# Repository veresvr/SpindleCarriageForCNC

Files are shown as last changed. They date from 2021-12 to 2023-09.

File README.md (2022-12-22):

# Spindle Carriage For CNC
:100: Project is done!

Milling carriage for my [laser CNC](https://github.com/veresvr/LaserCNCMachine)
All drawings available here [Drawings](https://github.com/veresvr/SpindleCarriageForCNC/tree/main/Drawings/AllDrawings.pdf)

##### Rendering
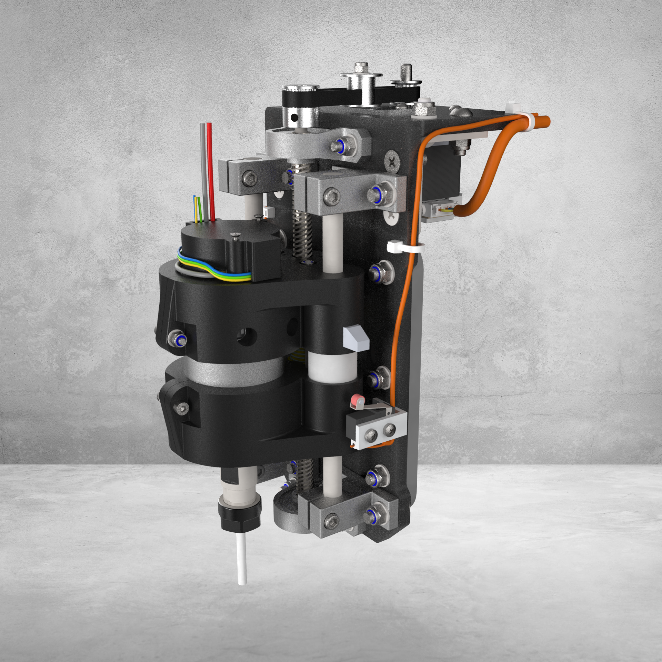
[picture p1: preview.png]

##### Assembly structure


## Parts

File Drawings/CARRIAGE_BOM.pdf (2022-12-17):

Project Spindle Carriage For CNC | Project Link GitHub (https://github.com/veresvr/SpindleCarriageForCNC)
Title cnc_milling_carriage_v1.SLDASM | Project Number 000
Designer Vladimir Tyrkin | Drawn by Vladimir Tyrkin
File CARRIAGE_BOM.xlsx
Date 17 December 2022 | Rev. 1
Dwg. | Item No. | Qty | Scem | Description | Material | Manufacturer | Part Number | Manufacturer Link | Weight | Total Weight
001 2 | | | | Linear Motion Shaft | 52100 Alloy Steel | McMaster-Carr | 5033N132 | McMaster-Carr (https://www.mcmaster.com/5033N132/) | 58.89 | 117.78
| | | | | | McMaster-Carr | 4920N11 | McMaster-Carr (https://www1.mcmaster.com/4920N11/)
| | | | | | CHINA | none | Aliexpress (https://aliexpress.ru/item/4001203233924.html?spm=a2g0o.detail.1000060.2.27ee4f0eyzRaOZ&gps-)
002 | 1 | 1 | | Lead Screw | AISI 1020 | CHINA | none | Aliexpress (https://aliexpress.ru/item/4001230970430.html?_ga=2.84334745.1452778018.1644222722-) | 62.17 | 62.17
| | | | Note: must be pair to item 2
011 1 | | | | Stepper Base | Polycarbonate (PC) | McMaster-Carr | 8574K281 | McMaster-Carr (https://www.mcmaster.com/8574K281/) | 37.88 | 37.88
| | | | Files: Drawings/parts for cnc.DWG & Drawings/parts for cnc.CDR
012 1 | | | | Vertical Plate | Polycarbonate (PC) | McMaster-Carr | 8574K281 | McMaster-Carr (https://www.mcmaster.com/8574K281/) | 120.14 | 120.14
| | | | Files: Drawings/parts for cnc.DWG & Drawings/parts for cnc.CDR
025 | | 2 | | ThreadedRodMotor | AISI 1035 Steel (SS) | McMaster-Carr | 94595A215 | McMaster-Carr (https://www.mcmaster.com/94595A215/) | 4.7 | 9.4
031 | | 1 | | TensionerBasePlate | 6061 Alloy | McMaster-Carr | 9146T14-9146T141 | McMaster-Carr (https://www.mcmaster.com/9146T14-9146T141/) | 4.5 | 4.5
032 | | 1 | | Standoff threaded round spacer | 6063-T6 | CHINA | none | Aliexpress (https://aliexpress.ru/item/32881933703.html?sku_id=12000022052244225&_ga=2.177706725.1570185891.1667054803-) | 0.48 | 0.48
081 | | 2 | | SensorMount | 6063-T6 | McMaster-Carr | 4630T135 | McMaster-Carr (https://www.mcmaster.com/4630T135/) | 2.19 | 4.38
None | | 2 | | Corner Bracket 40х40L | AISI 1035 Steel (SS) | Soberizavod | H49 | Soberizavod (https://www.soberizavod.ru/catalog/uglovye_soediniteli_seriya_20/ugolok_40kh20l_paz_6_h49/) | 49 | 98
None | | 4 | | SK8 SC8UU LINEAR RAIL ORIGINAL | Multimaterial | CHINA | none | Aliexpress (https://www.aliexpress.com/snapshot/0.html?orderId=5012744429362323&productId=32857642687) | 25 | 100
None | | 2 | | Pillow Block | Multimaterial | CHINA | none | Aliexpress (https://aliexpress.ru/item/4000176610214.html?_ga=2.180800559.940251345.1645298115-) | 37 | 74
None | | 2 | | Limit Switch | Multimaterial | DIGIKEY | none | DIGIKEY (https://www.digikey.com/en/products/detail/omron-electronics-inc-emc-div/ssg-01l2t-5/3102941) | 1.6 | 3.2
None | | 1 | | Nema 17HS4401 Stepper Motor | Multimaterial | CHINA | none | Aliexpress (https://aliexpress.ru/item/32665922113.html?_ga=2.134133639.847069604.1626648373-) | 315 | 315
None | | 5 | | Cable tie 3 mm width | Nylon 101 | McMaster-Carr | 7130K31 | McMaster-Carr (https://www.mcmaster.com/7130K31/) | 0.16 | 0.8
None | | 1 | | Belt | Rubber | CHINA | none | Aliexpress (https://aliexpress.ru/item/32971350055.html?sku_id=12000025662809083&_ga=2.102057921.1740671391.1667596887-) | 1.34 | 1.34
None | | 1 | | Heat shrink tube | Rubber | McMaster-Carr | 7496K85 | McMaster-Carr (https://www.mcmaster.com/7496K85/) | 0.12 | 0.12
None | | 1 | | Power cable 9Amp max. | Wire | McMaster-Carr | 9700T61 | McMaster-Carr (https://www.mcmaster.com/9700T61/) | 7.93 | 7.93
None | | 1 | | DC 775 Motor | Multimaterial | CHINA | none | Aliexpress (https://aliexpress.ru/item/32954455244.html?_ga=2.25715773.1065263870.1623483208-) | 314 | 314
None | | 2 | | 2GT 20Teeth Pulley | Multimaterial | CHINA | none | Aliexpress (https://aliexpress.ru/item/32969561177.html?sku_id=66708120873&_ga=2.26566781.1740671391.1667596887-) | 5.11 | 10.22
None | | 1 | | ER11 collet | Multimaterial | CHINA | none | Aliexpress (https://aliexpress.ru/item/33009204061.html?_ga=2.95643420.1065263870.1623483208-) | 49 | 49
None | | 1 | | Pulley 20T W10 B5 With Teeth | Multimaterial | CHINA | none | Aliexpress (https://aliexpress.ru/item/1005003836633631.html?sku_id=12000027307595864) | 10 | 10
None | | 4 | | LM8UU Lineare bearing | Multimaterial | CHINA | none | Aliexpress (https://aliexpress.ru/item/32317938156.html?_ga=2.97133343.1065263870.1623483208-) | 16 | 64
None | | 1 | | Cable Top End Sensor (230mm) | Multimaterial | McMaster-Carr | 9697T1 | McMaster-Carr (https://www.mcmaster.com/9697T1/) | 3.05 | 3.05
None | | 1 | | Cable Bottom End Sensor (290mm) | Multimaterial | McMaster-Carr | 9697T1 | McMaster-Carr (https://www.mcmaster.com/9697T1/) | 2.29 | 2.29
None | | 1 | | 3 CIRCUIT RECEPTACLE MOLEX | Multimaterial | MOUSER | none | Mouser (https://eu.mouser.com/ProductDetail/Molex/39-01-4031?qs=pAYFZ4D%2FDKsfbhxQKf4bKg%3D%3D) | 1 | 1
None | 2 | 1 | | Movement Nut | Brass | CHINA | none | Aliexpress (https://aliexpress.ru/item/32317938156.html?_ga=2.97133343.1065263870.1623483208-) | 11.5 | 11.5
| | | | Note: must be pair to item 1
Total weight | 1422.2
3D printed parts
021 | 1 | Bottom motor cover | PET-G | McMaster-Carr | 3462N1 | McMaster-Carr (https://www.mcmaster.com/3462N1/) | 93 | 93
| | File: FilesForPrint/Bottom motor cover.STL
022 | 1 | Top motor cover | PET-G | McMaster-Carr | 3462N1 | McMaster-Carr (https://www.mcmaster.com/3462N1/) | 87.98 | 87.98
| | File: FilesForPrint/Top motor cover.STL
024 | 2 | Spacer | PET-G | McMaster-Carr | 3462N1 | McMaster-Carr (https://www.mcmaster.com/3462N1/) | 5.97 | 11.94
| | File: FilesForPrint/Spacer.STL
026 1 | | Cable holder | PET-G | McMaster-Carr | 3462N1 | McMaster-Carr (https://www.mcmaster.com/3462N1/) | 1.21 | 1.21
| | File: FilesForPrint/WiresHolder.STL
Total weight | 194.13
Page 1 of 2 | 12/17/2022 16:02

Dwg. | Item
No. | Scem | Description | Material | Manufacturer | Part Number | Manufacturer Link
Weight

Total
Weight Qty

Screws
None | 1 | Self Tap. Cross recessed Screw 2.6x10mm | AISI 304 | CHINA | none | Aliexpress (https://aliexpress.ru/item/33040347870.html?spm=a2g0s.9042311.0.0.274233edM7ZVS8) | 0.23 | 0.23
None | 6 | M3 NYLOC DIN 985 | AISI 304 | CHINA | none | Aliexpress (https://www.mcmaster.com/nuts/locknuts/metric-18-8-stainless-steel-nylon-insert-locknuts/) | 0.65 | 3.9
None | 4 | M4 NYLOC DIN 985 | AISI 304 | McMaster-Carr | none | McMaster-Carr (https://www.mcmaster.com/nuts/locknuts/metric-18-8-stainless-steel-nylon-insert-locknuts/) | 1.29 | 5.16
None | 22 | M5 NYLOC DIN 985 | AISI 304 | McMaster-Carr | none | McMaster-Carr (https://www.mcmaster.com/nuts/locknuts/metric-18-8-stainless-steel-nylon-insert-locknuts/) | 1.6 | 35.2
None | 6 | Low Profile Hex Screw M5x30 | AISI 1035 Steel (SS) | CHINA | none | Aliexpress (https://aliexpress.ru/item/4001232036314.html?_ga=2.27484988.1065263870.1623483208-) | 3.63 | 21.78
| | | | McMaster-Carr | none | McMaster-Carr (https://www.mcmaster.com/90358A119/)
None | 4 | Rounded Head Thread-Forming Screw M3x20mm | 18-8 Stainless Steel | McMaster-Carr | 99461A947 | McMaster-Carr (https://www.mcmaster.com/99461A947/) | 0.73 | 2.92
None | 1 | M5x20 DIN 7991, ISO 10642 | 18-8 Stainless Steel | McMaster-Carr | 92125A214 | McMaster-Carr (https://www.mcmaster.com/92125A214/) | 3.162 | 3.162
None | 4 | M5x16 DIN 7991, ISO 10642 | 18-8 Stainless Steel | McMaster-Carr | 92125A212 | McMaster-Carr (https://www.mcmaster.com/92125A212/) | 2.65 | 10.6
None | 4 | ISO 4762 M4 x 20 - 20N | 18-8 Stainless Steel | McMaster-Carr | 91292A121 | McMaster-Carr (https://www1.mcmaster.com/91292A121/) | 2.65 | 10.6
None | 17 | Washer DIN 125 - A 5.3 | Zinc Plated Steel | McMaster-Carr | none | McMaster-Carr (https://www1.mcmaster.com/standard-washers/washers-4/washers-5/metric-general-purpose-washers/) | 0.44 | 7.48
None | 4 | Washer DIN 125 - A 4.3 | Zinc Plated Steel | McMaster-Carr | none | McMaster-Carr (https://www1.mcmaster.com/standard-washers/washers-4/washers-5/metric-general-purpose-washers/) | 0.3 | 1.2
None | 7 | Washer DIN 125 - A 3.2 | Zinc Plated Steel | McMaster-Carr | 91166A210 | McMaster-Carr (https://www1.mcmaster.com/91166A210/) | 0.12 | 0.84
None | 2 | ISO 4762 M3 x 16 - 16N | 18-8 Stainless Steel | McMaster-Carr | none | McMaster-Carr (https://www.mcmaster.com/screws/socket-head-screws/socket-head-screws-6/18-8-stainless-steel-socket-head-screws-11/system-of-measurement~metric/) | 1.16 | 2.32
None | 2 | ISO 7380 - M3 x 10 - 10N | 316 Stainless Steel | McMaster-Carr | 90943A113 | McMaster-Carr (https://www.mcmaster.com/90943A113/) | 0.7 | 1.4
None | 4 | ISO 7380 - M5 x 16 - 16N | 18-8 Stainless Steel | McMaster-Carr | 92095A212 | McMaster-Carr (https://www.mcmaster.com/92095A212/) | 2.9 | 11.6
None | 3 | ISO 7380 - M3 x 8 - 8N | 18-8 Stainless Steel | McMaster-Carr | 92095A181 | McMaster-Carr (https://www1.mcmaster.com/92095A181/) | 0.6 | 1.8
None | 3 | ISO 7046-1 - M3 x 8 - Z - 8N | 18-8 Stainless Steel | McMaster-Carr | 92010A118 | McMaster-Carr (https://www1.mcmaster.com/92010A118/) | 0.47 | 1.41
None | 4 | ISO 7046-1 - M3 x 10 - Z - 10N | 18-8 Stainless Steel | McMaster-Carr | For DIN 965: 92010A120 | McMaster-Carr (https://www1.mcmaster.com/92010A120/) | 0.53 | 2.12
None | 4 | DIN EN ISO 7045 - M3 x 10 - Z - 10N | Zinc-Plated Steel | McMaster-Carr | 92005A120 | McMaster-Carr (https://www1.mcmaster.com/92005A120/) | 1.27 | 5.08
None | 4 | ISO 7046-1 - M5 x 20 - Z - 20N | Zinc-Plated Steel | McMaster-Carr | For DIN 965: 91420A328 | McMaster-Carr (https://www.mcmaster.com/91420A328/) | 2.86 | 11.44
Total weight | 140.24
Page 2 of 2 | 12/17/2022 16:02

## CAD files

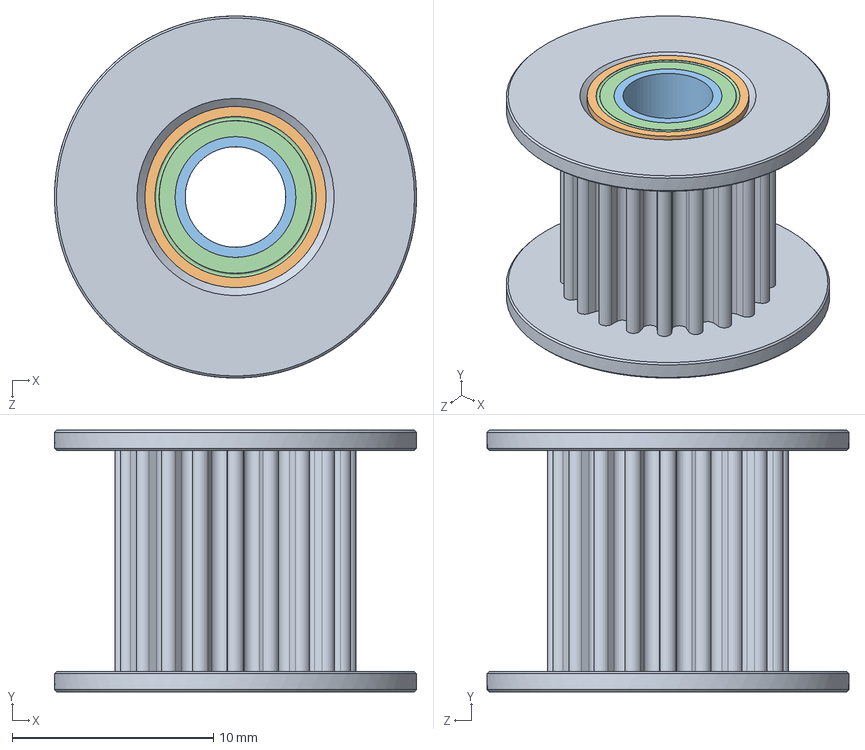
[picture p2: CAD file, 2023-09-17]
3D/GT2 Idler Pulley, Configurable.SLDASM
18.0 x 13.0 x 18.0 mm
Body, GT2 Idler Pulley, Configurable
Bearing Outer Ring, GT2 Idler Pulley, Configurable x 2
Bearing Inner Ring, GT2 Idler Pulley, Configurable x 2
Bearing Seal, GT2 Idler Pulley, Configurable x 4
Bearing Ball, GT2 Idler Pulley, Configurable x 22

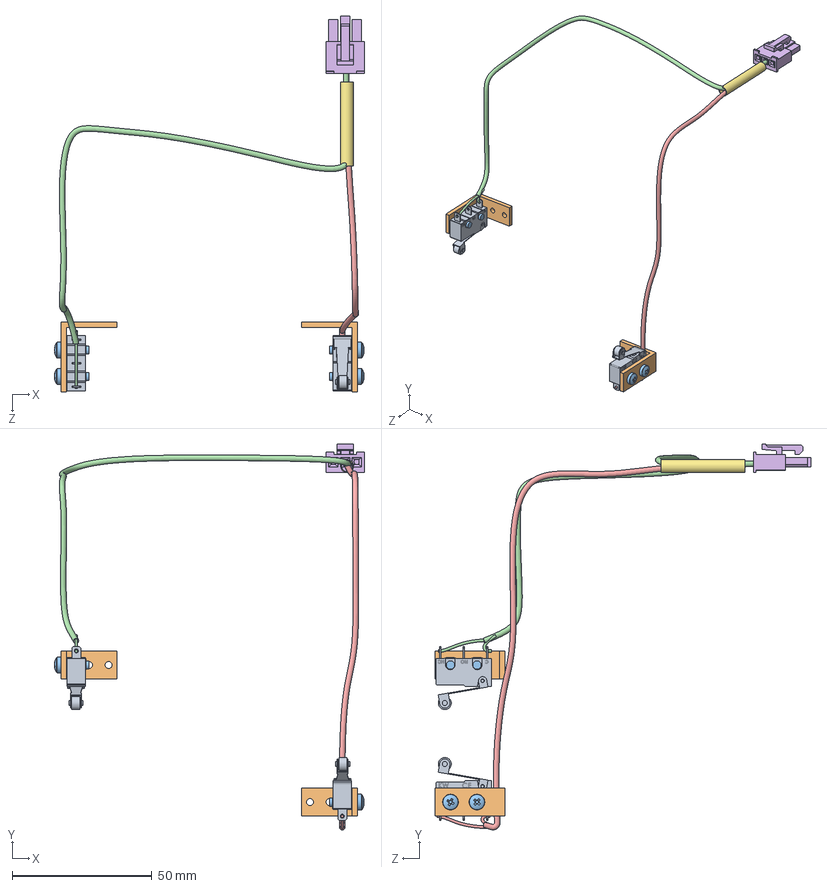
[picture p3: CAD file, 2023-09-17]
3D/SensorsAssembly.SLDASM
110.8 x 138.0 x 134.4 mm
Limit Switch x 2
SensorMount x 2
pan head cross recess screw_din x 4
CableTopEndSensor^SensorsAssembly
CableBottomEndSensor^SensorsAssembly
3 CIRCUIT RECEPTACLE MOLEX
Heat-Shrink Tube^SensorsAssembly

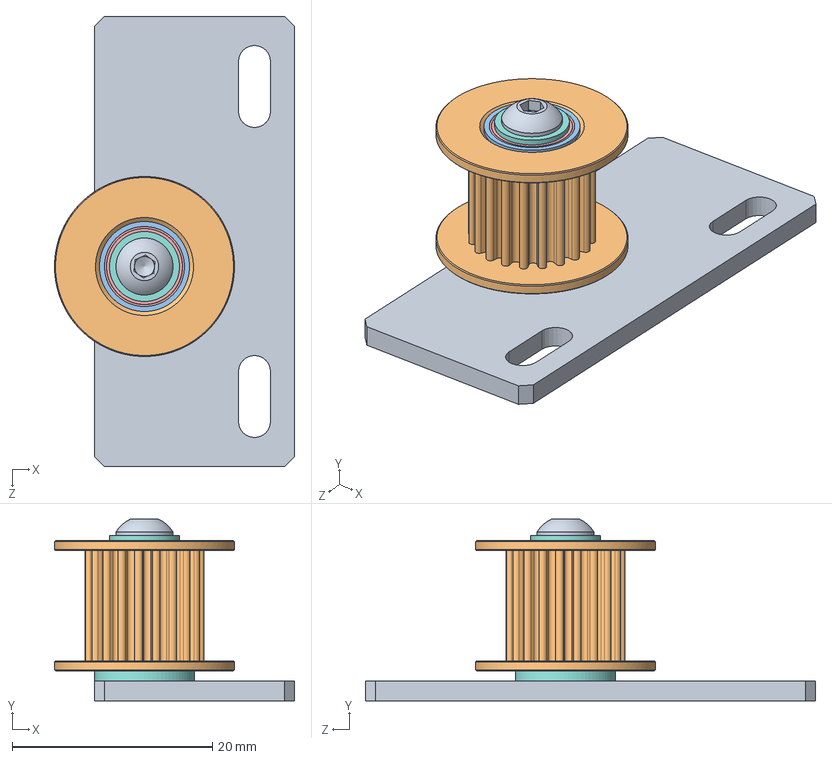
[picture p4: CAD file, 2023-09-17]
3D/Tensioner.SLDASM
24.0 x 18.1 x 45.0 mm
TensionerBasePlate
Body, GT2 Idler Pulley, Configurable
Bearing Outer Ring, GT2 Idler Pulley, Configurable x 2
Bearing Inner Ring, GT2 Idler Pulley, Configurable x 2
Bearing Seal, GT2 Idler Pulley, Configurable x 4
Bearing Ball, GT2 Idler Pulley, Configurable x 22
countersunk flat head cross recess screw_iso
plain washer grade a_din x 2
socket button head screw_iso
Standoff threaded round spacer

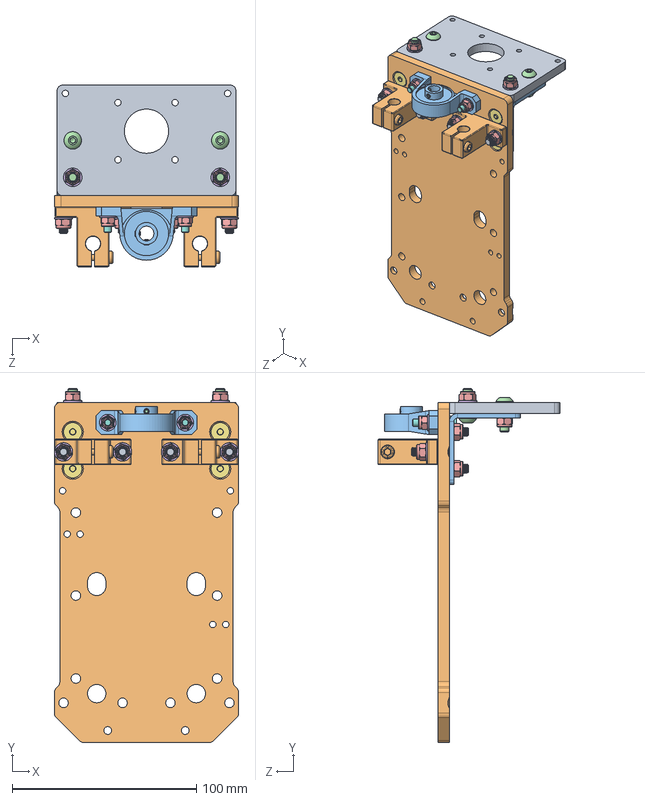
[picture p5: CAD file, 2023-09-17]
3D/CarriageBase.SLDASM
100.0 x 192.0 x 98.6 mm
Stepper Base
Vertical Plate
Corner Bracket 40х40L x 2
socket button head screw_iso x 4
Nyloc nut St_Steel A2 ISO M2_5-M36 x 14
plain washer grade a_din x 8
92125A212_18-8 Stainless Steel Hex Drive Flat Head Screw x 4
socket head cap screw_iso x 2
92125A214_18-8 Stainless Steel Hex Drive Flat Head Screw x 4
SK8 SC8UU LINEAR RAIL ORIGINAL x 2
Pillow Block KP08
socket set screw flat point_iso x 2

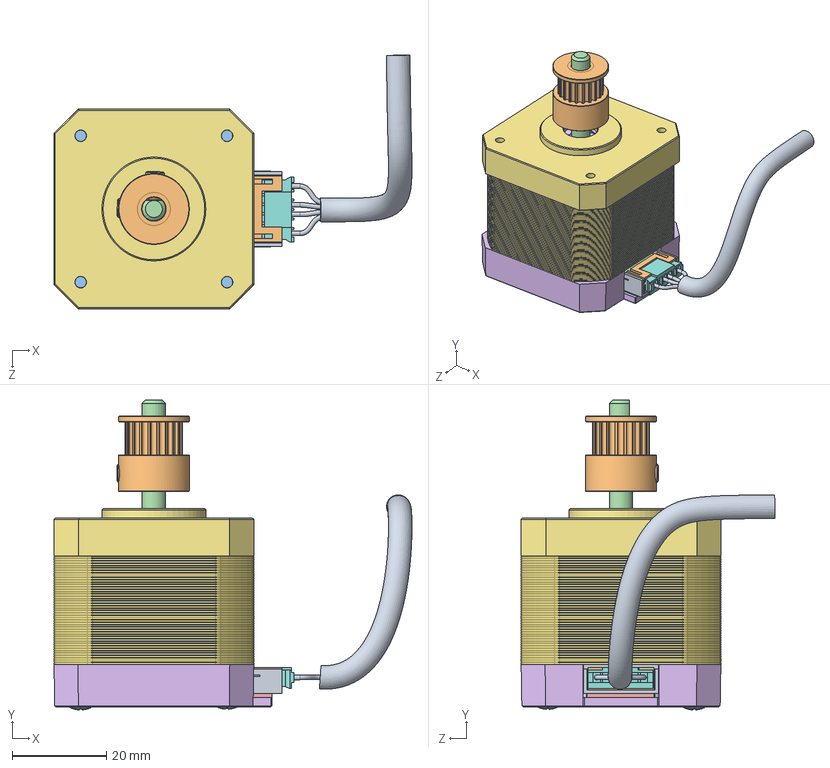
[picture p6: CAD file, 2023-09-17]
3D/Stepper Assembly.SLDASM
75.8 x 65.6 x 53.7 mm
BS 3469 - 02 - 5 x 16 x 5^Nema 17HS4401 Stepper Motor x 2
Nema 17 Plastic Spacer 2^Nema 17HS4401 Stepper Motor
Nema 17 Plastic Spacer 1
Nema 17 shaft^Nema 17HS4401 Stepper Motor
ANSI B27.7 - 5, E^Nema 17HS4401 Stepper Motor
Nema 17 Base Cap^Nema 17HS4401 Stepper Motor
Nema 17 Central Spacer^Nema 17HS4401 Stepper Motor
Nema 17 Stator Face^Nema 17HS4401 Stepper Motor
Nema 17 plastic^Nema 17HS4401 Stepper Motor
S6B-PH-K-S^Nema 17HS4401 Stepper Motor
EN ISO 7045 - M3 x 25(1)^Nema 17HS4401 Stepper Motor x 4
Nema 17 plastic protector^Nema 17HS4401 Stepper Motor
Nema 17 PCB^Nema 17HS4401 Stepper Motor
Nema 17 Sprung Washer^Nema 17HS4401 Stepper Motor
17HS4401-Part5^Nema 17HS4401 Stepper Motor
PHR-6-connector
Part1^CableStepperY_Stepper Assembly
2GT_20T_Toothed_5mmBore

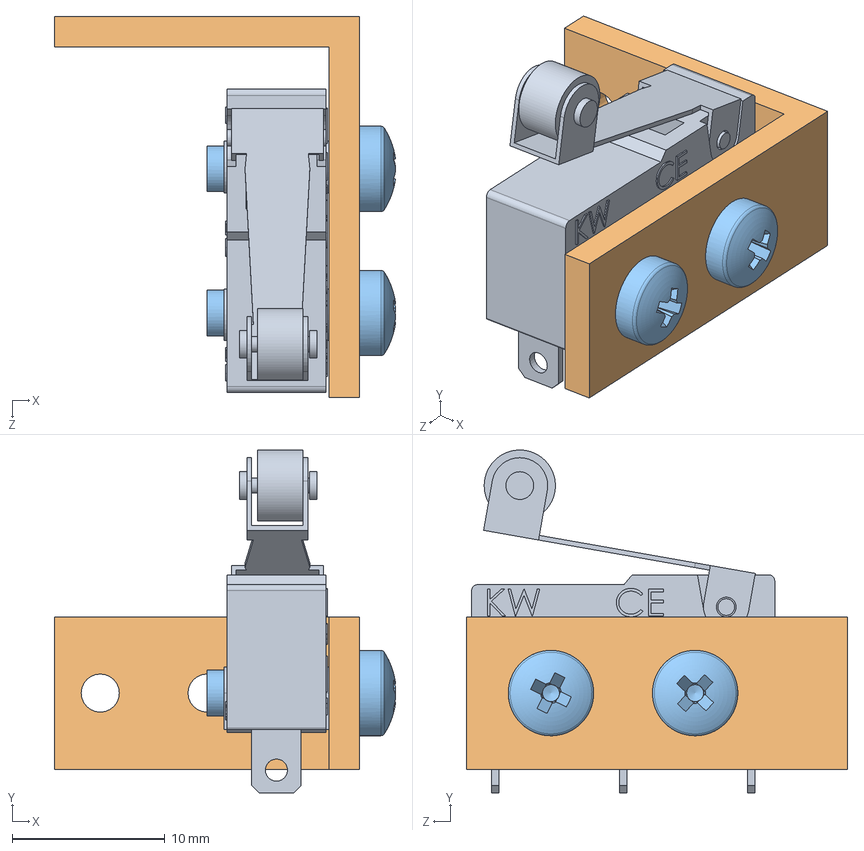
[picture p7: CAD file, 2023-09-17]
3D/EndSensorModule.SLDASM
22.4 x 22.5 x 25.0 mm
Limit Switch
SensorMount
pan head cross recess screw_din x 2

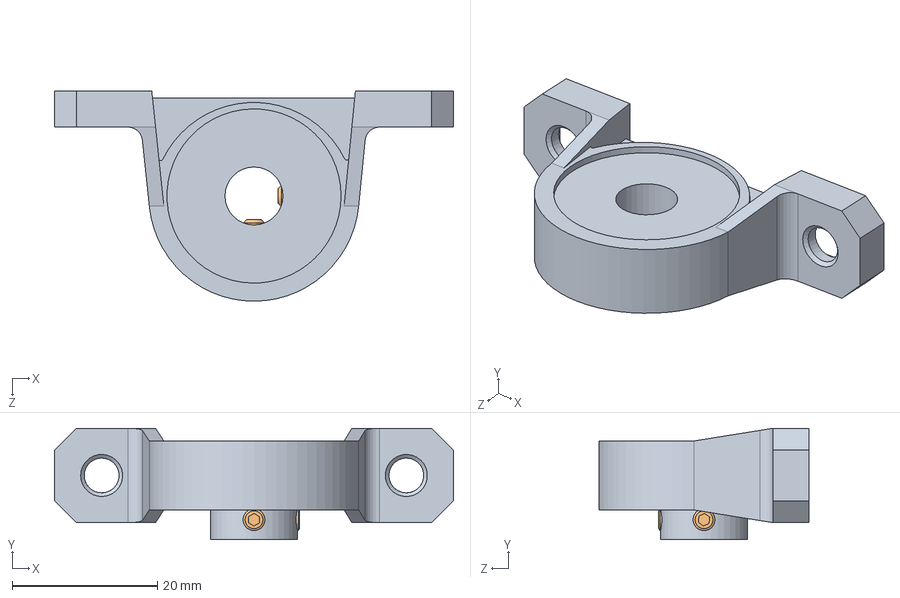
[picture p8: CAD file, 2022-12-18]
3D/PillowBlockAssembly.SLDASM
55.0 x 15.4 x 29.0 mm
Pillow Block KP08
socket set screw flat point_iso x 2

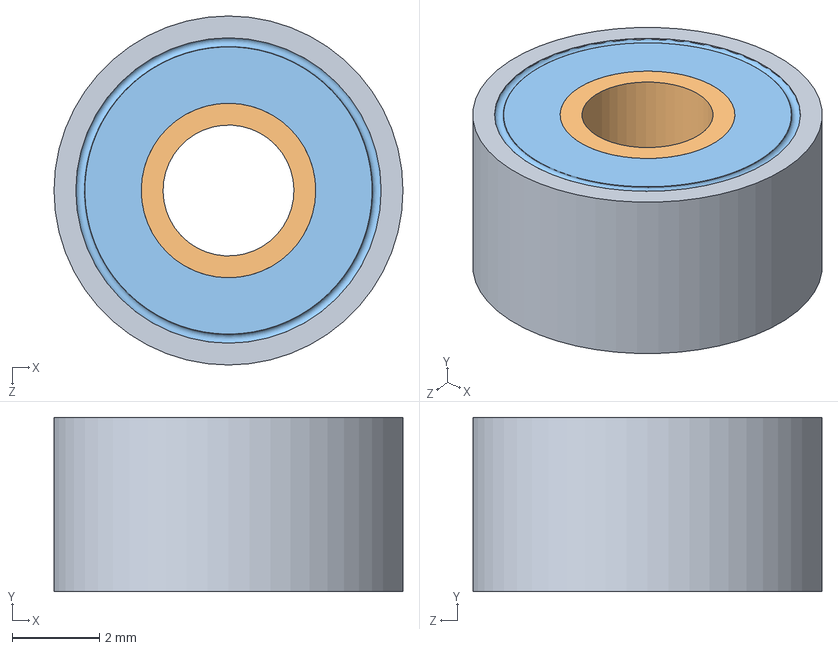
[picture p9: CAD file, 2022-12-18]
3D/Bearing Subassy, GT2 Idler Pulley, Configurable.SLDASM
8.00 x 4.00 x 8.00 mm
Bearing Outer Ring, GT2 Idler Pulley, Configurable
Bearing Inner Ring, GT2 Idler Pulley, Configurable
Bearing Seal, GT2 Idler Pulley, Configurable x 2
Bearing Ball, GT2 Idler Pulley, Configurable x 6

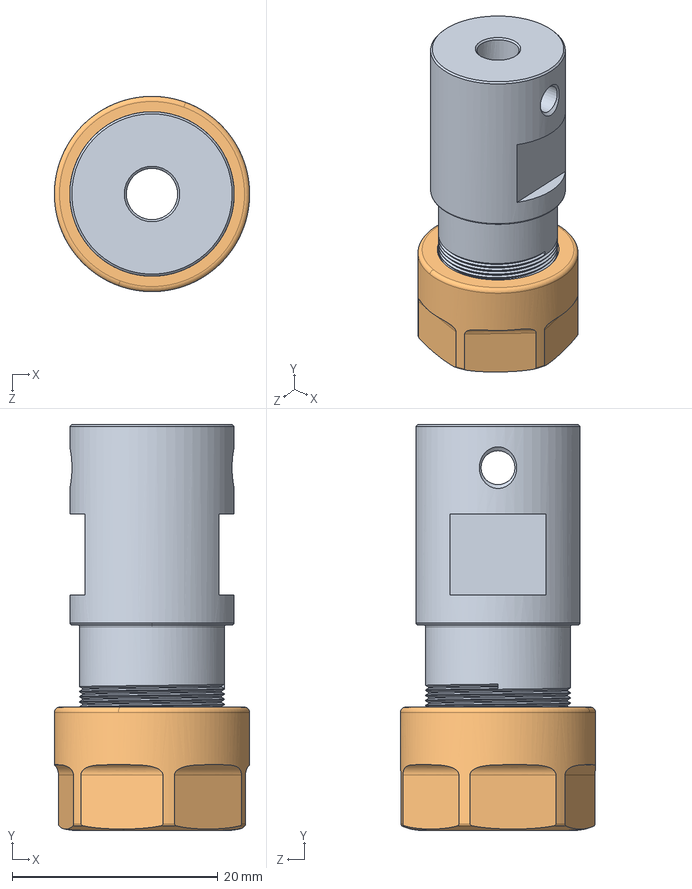
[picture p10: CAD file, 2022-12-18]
3D/ER11 collet.SLDASM
19.0 x 39.5 x 19.0 mm
ER11 - Collet Chuck
ER11 - Nut - Type A

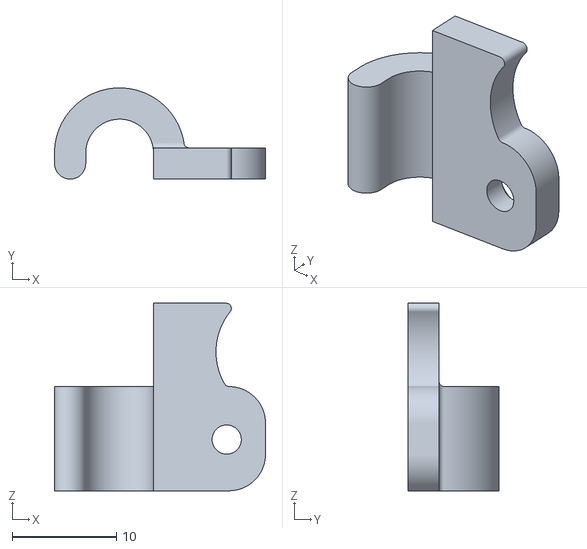
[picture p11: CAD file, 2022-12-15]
FilesForPrint/CableHolder.STL
20.3 x 8.75 x 18.0

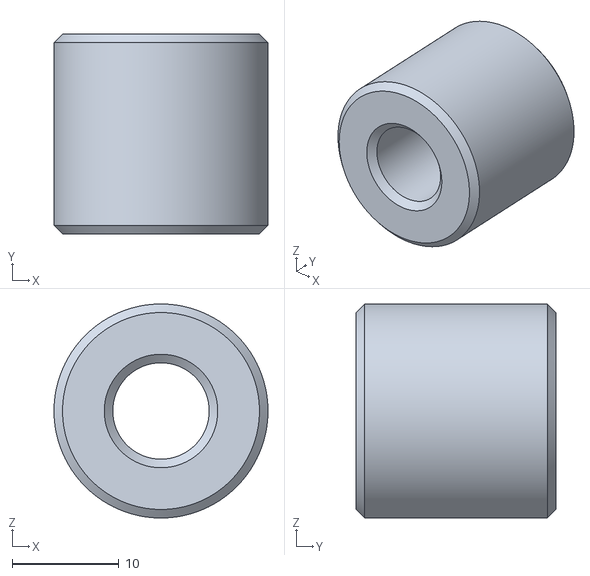
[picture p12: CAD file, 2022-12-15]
FilesForPrint/Spacer.STL
20.0 x 18.7 x 20.0

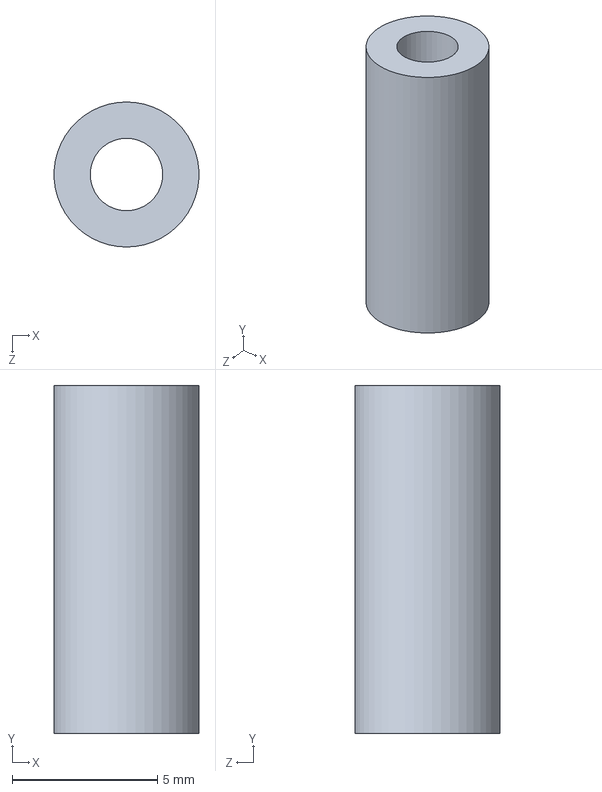
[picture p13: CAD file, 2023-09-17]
3D/Standoff threaded round spacer.SLDPRT
4.99 x 12.0 x 5.00 mm

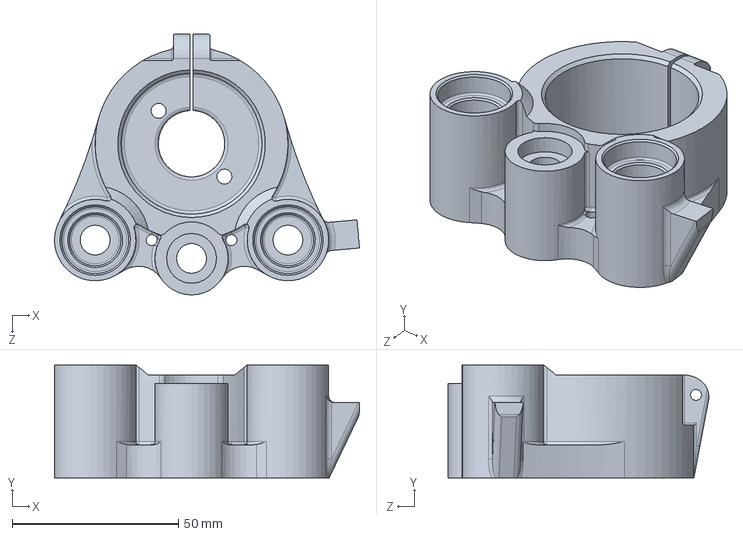
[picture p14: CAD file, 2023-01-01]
3D/Bottom motor cover.SLDPRT
91.8 x 34.0 x 78.5 mm

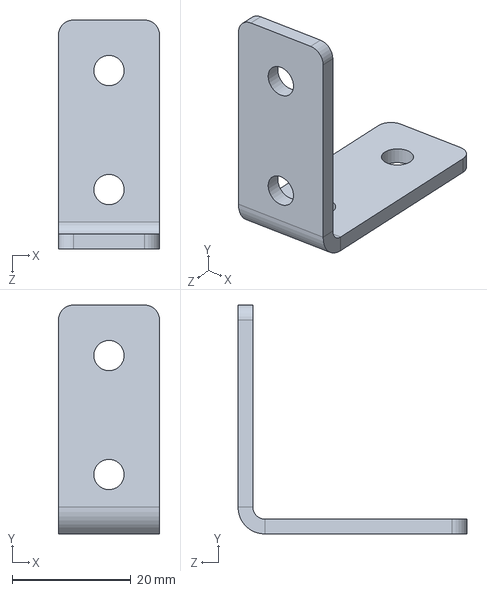
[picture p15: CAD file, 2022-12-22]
3D/Corner Bracket 40х40L.SLDPRT
17.0 x 38.5 x 38.5 mm

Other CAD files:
Drawings/parts for cnc.DWG
3D/Top motor cover.SLDPRT
3D/2GT_20T_Toothed_5mmBore.SLDPRT
3D/3 CIRCUIT RECEPTACLE MOLEX.SLDPRT
3D/92125A212_18-8 Stainless Steel Hex Drive Flat Head Screw.SLDPRT
3D/92125A214_18-8 Stainless Steel Hex Drive Flat Head Screw.SLDPRT
3D/99461A947_Phillips Rounded Head Thread-Forming Screws.SLDPRT
3D/Bearing Ball, GT2 Idler Pulley, Configurable.SLDPRT
3D/Bearing Inner Ring, GT2 Idler Pulley, Configurable.SLDPRT
3D/Bearing Outer Ring, GT2 Idler Pulley, Configurable.SLDPRT
3D/Bearing Seal, GT2 Idler Pulley, Configurable.SLDPRT
3D/Body, GT2 Idler Pulley, Configurable.SLDPRT
3D/CableHolder.SLDPRT
3D/Carriage Y_2 JustForReference.SLDPRT
3D/ER11 - Collet Chuck.SLDPRT
3D/ER11 - Nut - Type A.SLDPRT
3D/Lead Screw.sldprt
3D/Limit Switch.SLDPRT
3D/Linear Motion Shaft.SLDPRT
3D/Lineare_bearing_LMUU_serie.SLDPRT
3D/Low Profile Hex Screw M5.SLDPRT
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

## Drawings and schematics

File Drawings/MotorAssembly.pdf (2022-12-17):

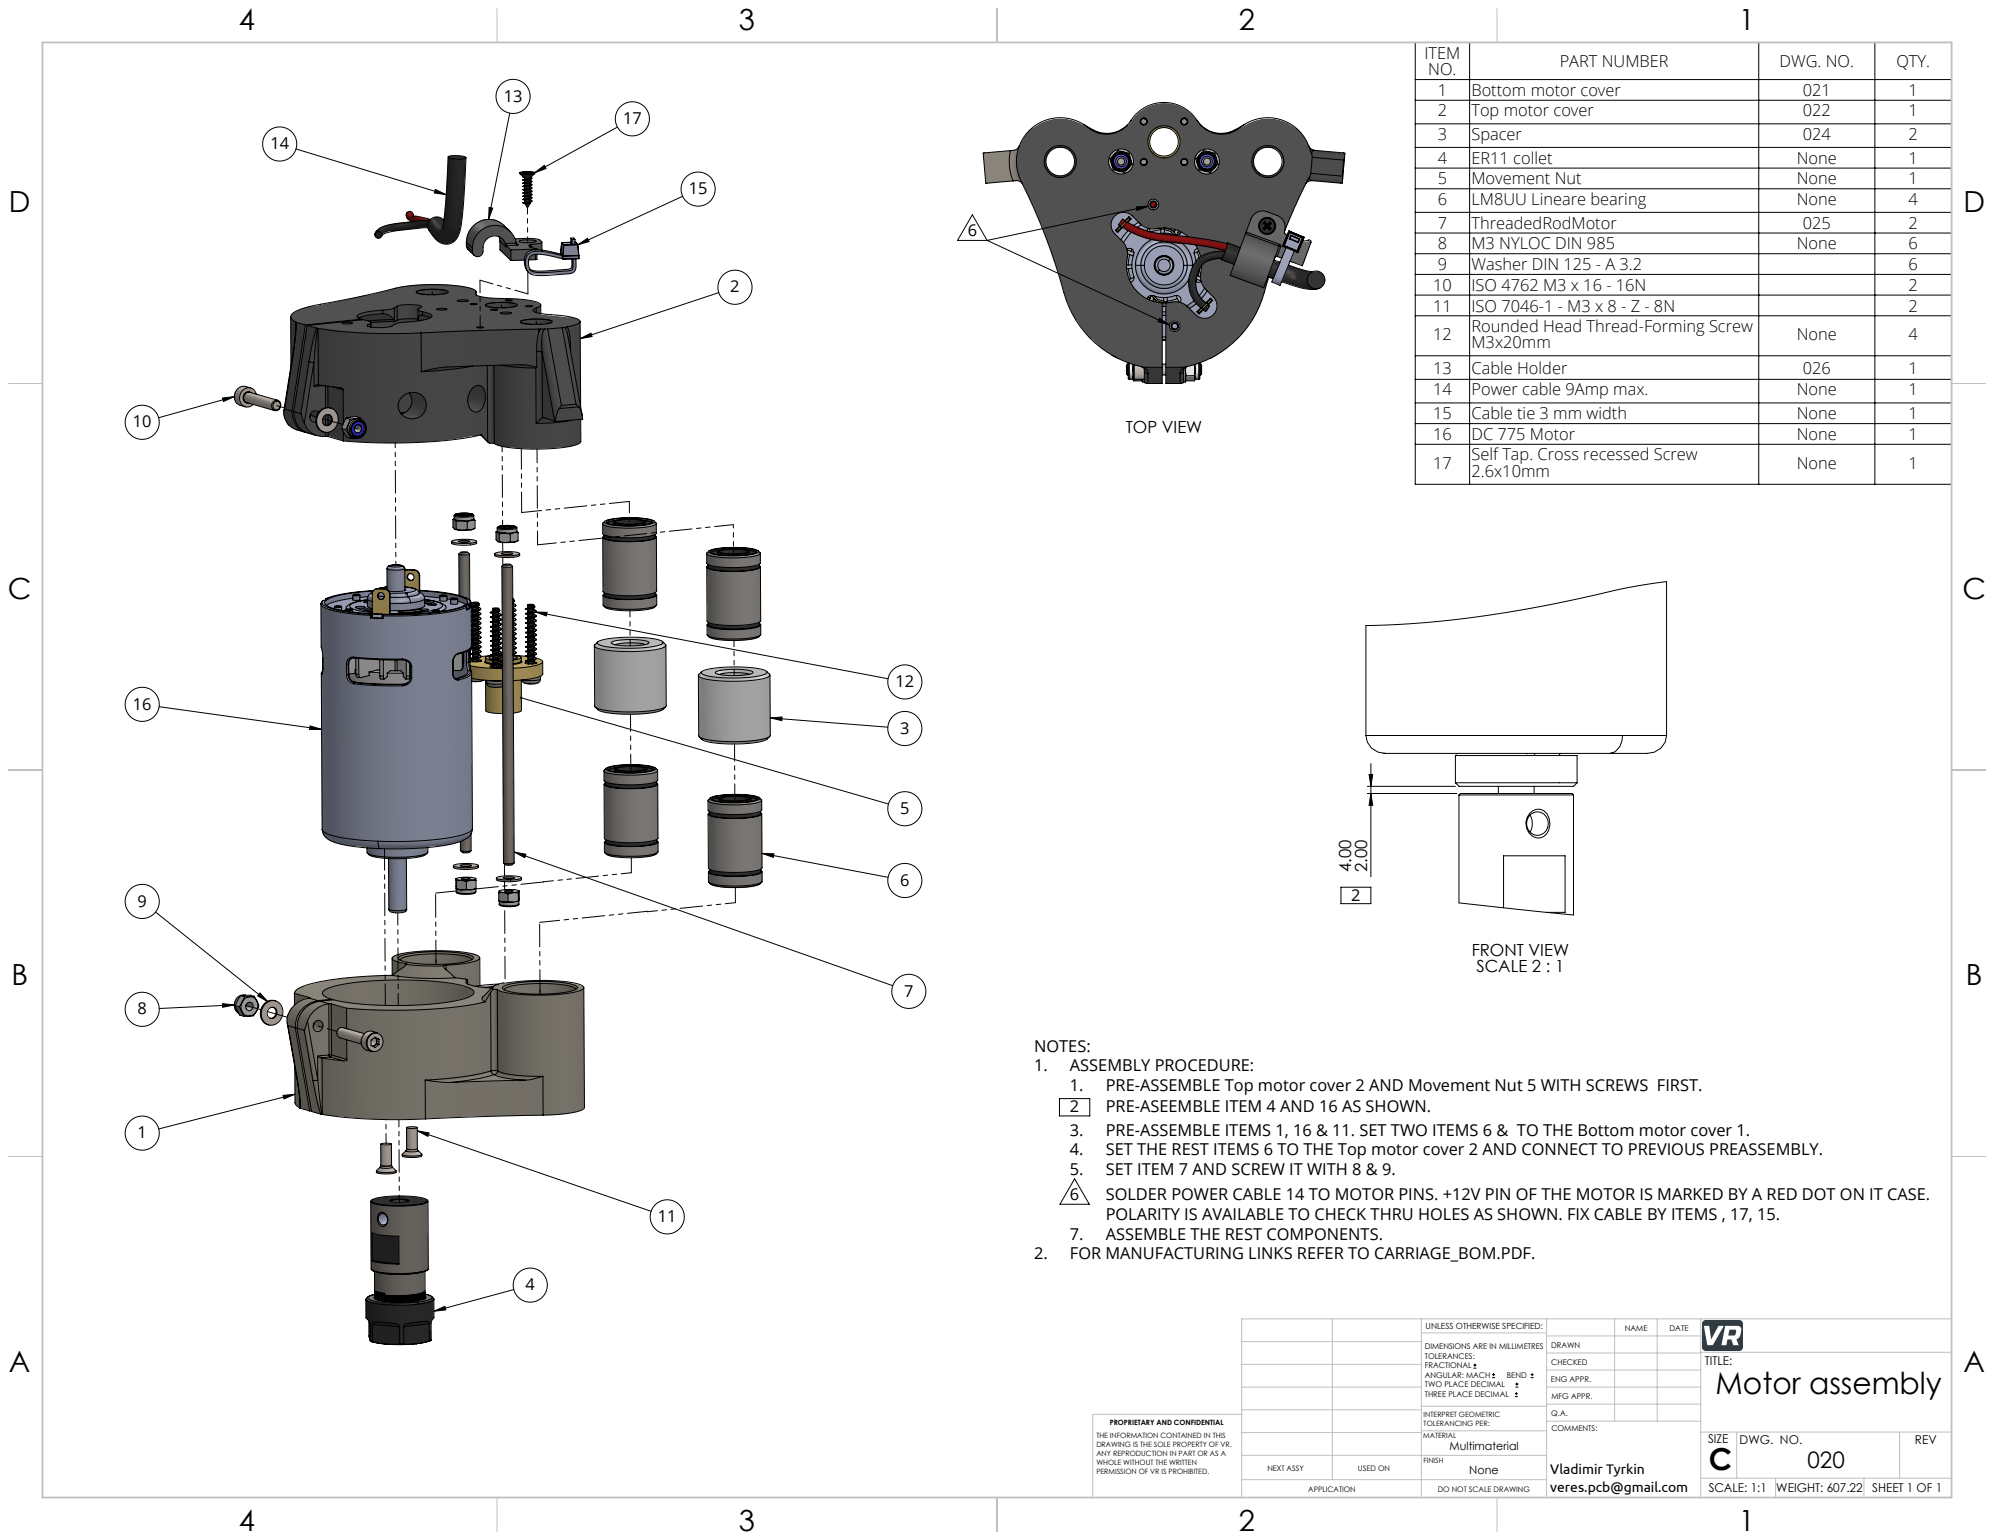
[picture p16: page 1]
TOP VIEW; FRONT VIEW SCALE 2 : 1; PRE-ASEEMBLE ITEM; SOLDER POWER CABLE 14 TO MOTOR PINS. +12V PIN OF THE MOTOR IS MARKED BY A RED DOT ON IT CASE.; PART NUMBER; DWG. NO.; QTY. 1; Bottom motor cover; Top motor cover; Spacer; ER11 collet; None; Movement Nut; LM8UU Lineare bearing; ThreadedRodMotor; M3 NYLOC DIN 985; Washer DIN 125 - A 3.2; REV; Vladimir Tyrkin

10 | ISO 4762 M3 x 16 - 16N | | 2
11 | ISO 7046-1 - M3 x 8 - Z - 8N | | 2
12 | Rounded Head Thread-Forming Screw M3x20mm | None | 4

13 | Cable Holder | 026 | 1
14 | Power cable 9Amp max. | None | 1
15 | Cable tie 3 mm width | None | 1
16 | DC 775 Motor | None | 1
17 | Self Tap. Cross recessed Screw 2.6x10mm | None | 1

NOTES:
1. ASSEMBLY PROCEDURE:
1. PRE-ASSEMBLE Top motor cover
3. PRE-ASSEMBLE ITEMS 1, 16 & 11. SET TWO ITEMS
4. SET THE REST ITEMS
5. SET ITEM
POLARITY IS AVAILABLE TO CHECK THRU HOLES AS SHOWN. FIX CABLE BY ITEMS , 17, 15
7. ASSEMBLE THE REST COMPONENTS.
2. FOR MANUFACTURING LINKS REFER TO CARRIAGE_BOM.PDF.

2 AND Movement Nut

5 WITH SCREWS FIRST.

4 AND 16 AS SHOWN.

6 & TO THE Bottom motor cover
2 AND CONNECT TO PREVIOUS PREASSEMBLY.

6 TO THE Top motor cover

7 AND SCREW IT WITH

UNLESS OTHERWISE SPECIFIED: | | NAME | DATE
DIMENSIONS ARE IN MILLIMETRES TOLERANCES: FRACTIONAL ANGULAR: MACH BEND TWO PLACE DECIMAL THREE PLACE DECIMAL | DRAWN

CHECKED | | | TITLE: Motor assembly

ENG APPR.
MFG APPR.

INTERPRET GEOMETRIC TOLERANCING PER: | Q.A.

PROPRIETARY AND CONFIDENTIAL
THE INFORMATION CONTAINED IN THIS
DRAWING IS THE SOLE PROPERTY OF VR.
ANY REPRODUCTION IN PART OR AS A
WHOLE WITHOUT THE WRITTEN
PERMISSION OF VR IS PROHIBITED.

NEXT ASSY | USED ON | None FINISH

APPLICATION | DO NOT SCALE DRAWING | | SCALE: 1:1 | WEIGHT: 607.22 | SHEET 1 OF 1

veres.pcb@gmail.com

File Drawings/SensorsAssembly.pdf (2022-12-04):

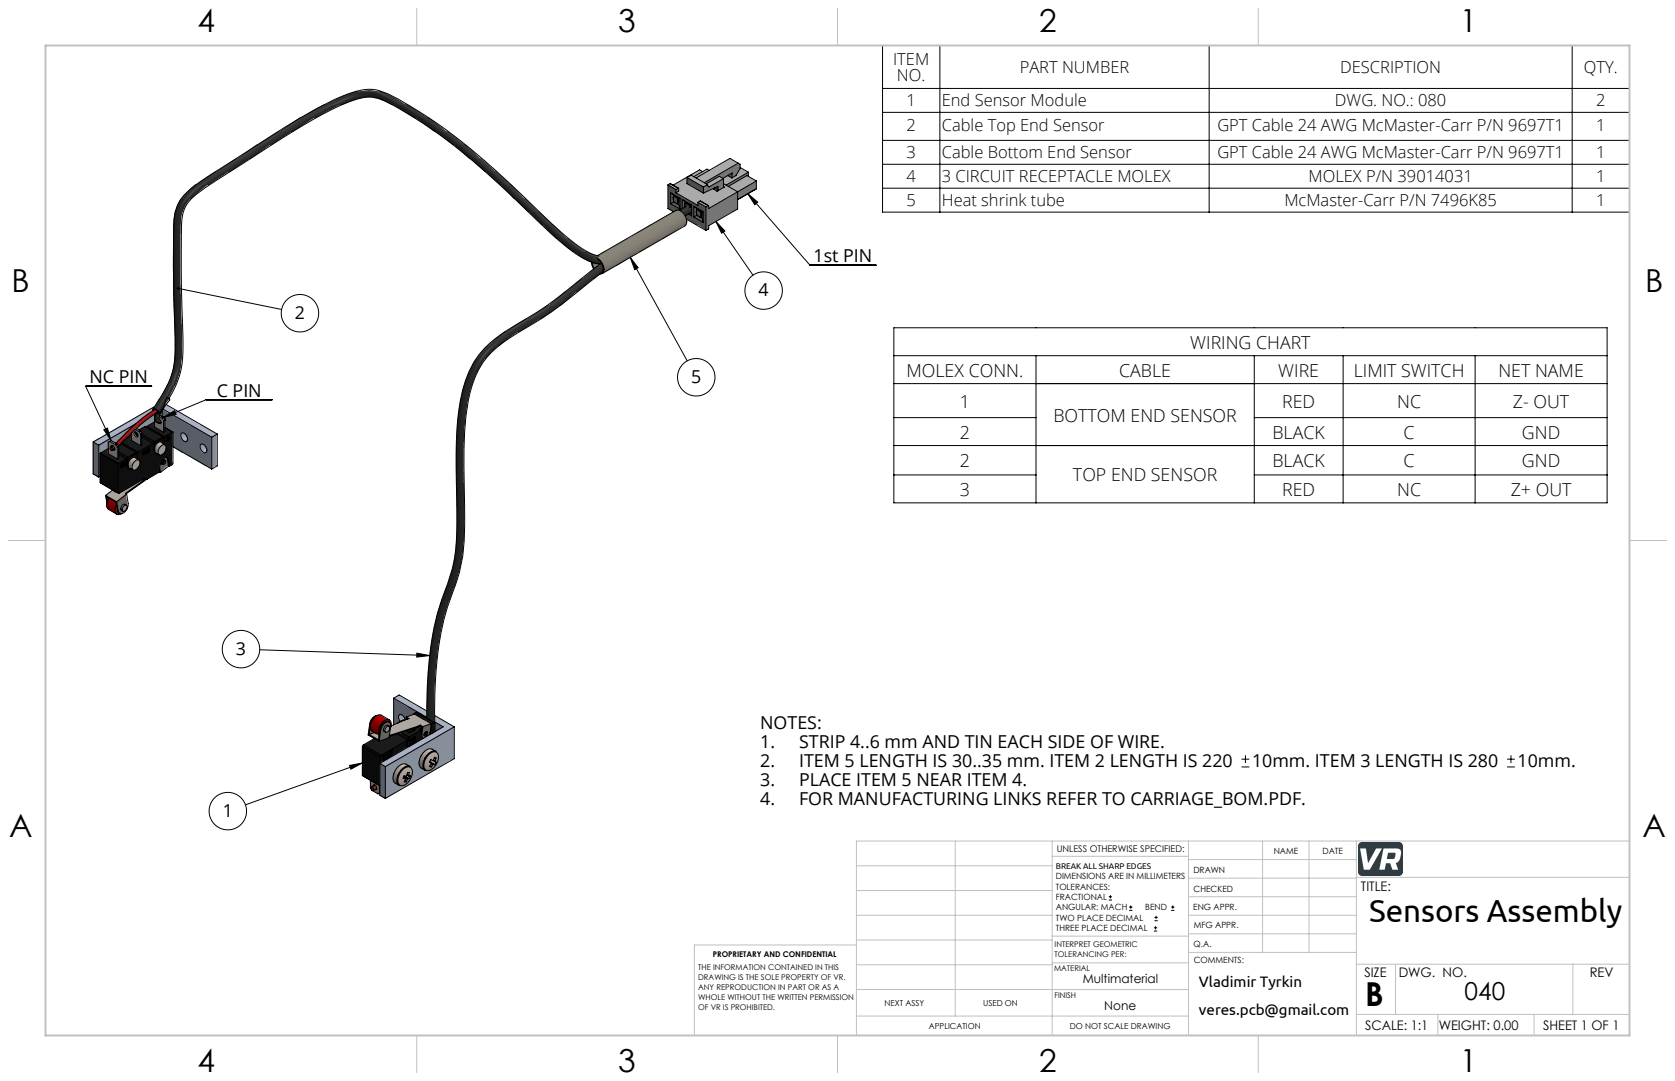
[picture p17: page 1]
1st PIN; C PIN; NC PIN; 2. ITEM 5 LENGTH IS 30..35 mm. ITEM 2 LENGTH IS 220; 10mm. ITEM 3 LENGTH IS 280; WIRING CHART; OF VR IS PROHIBITED.; veres.pcb@gmail.com; Vladimir Tyrkin

ITEM NO. | PART NUMBER | DESCRIPTION | QTY.
1 | End Sensor Module | DWG. NO.: 080 | 2
2 | Cable Top End Sensor | GPT Cable 24 AWG McMaster-Carr P/N 9697T1 | 1
3 | Cable Bottom End Sensor | GPT Cable 24 AWG McMaster-Carr P/N 9697T1 | 1
4 | 3 CIRCUIT RECEPTACLE MOLEX | MOLEX P/N 39014031 | 1
5 | Heat shrink tube | McMaster-Carr P/N 7496K85 | 1

MOLEX CONN. | CABLE | WIRE | LIMIT SWITCH | NET NAME
1 | BOTTOM END SENSOR | RED | NC | Z- OUT
2 | | BLACK | C | GND
2 | TOP END SENSOR | BLACK | C | GND
3 | | RED | NC | Z+ OUT

NOTES:
1. STRIP 4..6 mm AND TIN EACH SIDE OF WIRE.
3. PLACE ITEM 5 NEAR ITEM 4.
4. FOR MANUFACTURING LINKS REFER TO CARRIAGE_BOM.PDF.

UNLESS OTHERWISE SPECIFIED: | | NAME | DATE
BREAK ALL SHARP EDGES DIMENSIONS ARE IN MILLIMETERS TOLERANCES: FRACTIONAL ANGULAR: MACH BEND TWO PLACE DECIMAL THREE PLACE DECIMAL | DRAWN

CHECKED | | | TITLE: Sensors Assembly

ENG APPR.
MFG APPR.

INTERPRET GEOMETRIC TOLERANCING PER: | Q.A.
MATERIAL Multimaterial | | SIZE B | DWG. NO. 040 | REV

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

NEXT ASSY | USED ON | None FINISH

APPLICATION | DO NOT SCALE DRAWING | | SCALE: 1:1 | WEIGHT: 0.00 | SHEET 1 OF 1

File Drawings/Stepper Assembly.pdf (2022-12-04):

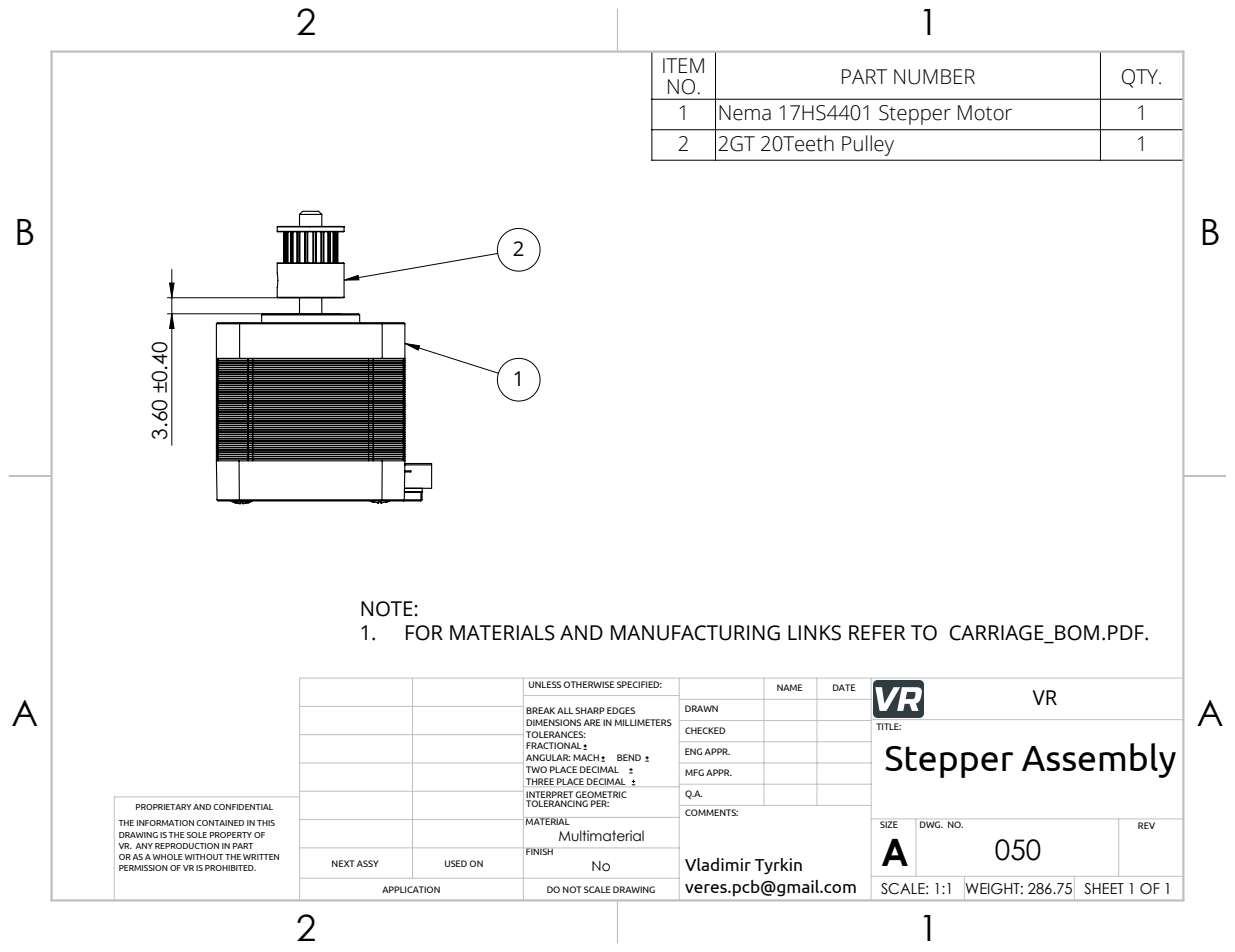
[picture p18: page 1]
PERMISSION OF VR IS PROHIBITED.; Vladimir Tyrkin

ITEM NO. | PART NUMBER | QTY.
1 | Nema 17HS4401 Stepper Motor | 1
2 | 2GT 20Teeth Pulley | 1

NOTE:
1. FOR MATERIALS AND MANUFACTURING LINKS REFER TO CARRIAGE_BOM.PDF.

UNLESS OTHERWISE SPECIFIED: | | DATE | VR NAME

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

CHECKED | | TITLE: Stepper Assembly

ENG APPR.

MFG APPR.

INTERPRET GEOMETRIC TOLERANCING PER: | Q.A.
MATERIAL Multimaterial | | SIZE A | DWG. NO. 050 | REV

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

NEXT ASSY | USED ON | FINISH No

APPLICATION | DO NOT SCALE DRAWING | | SCALE: 1:1 | WEIGHT: 286.75 | SHEET 1 OF 1

veres.pcb@gmail.com

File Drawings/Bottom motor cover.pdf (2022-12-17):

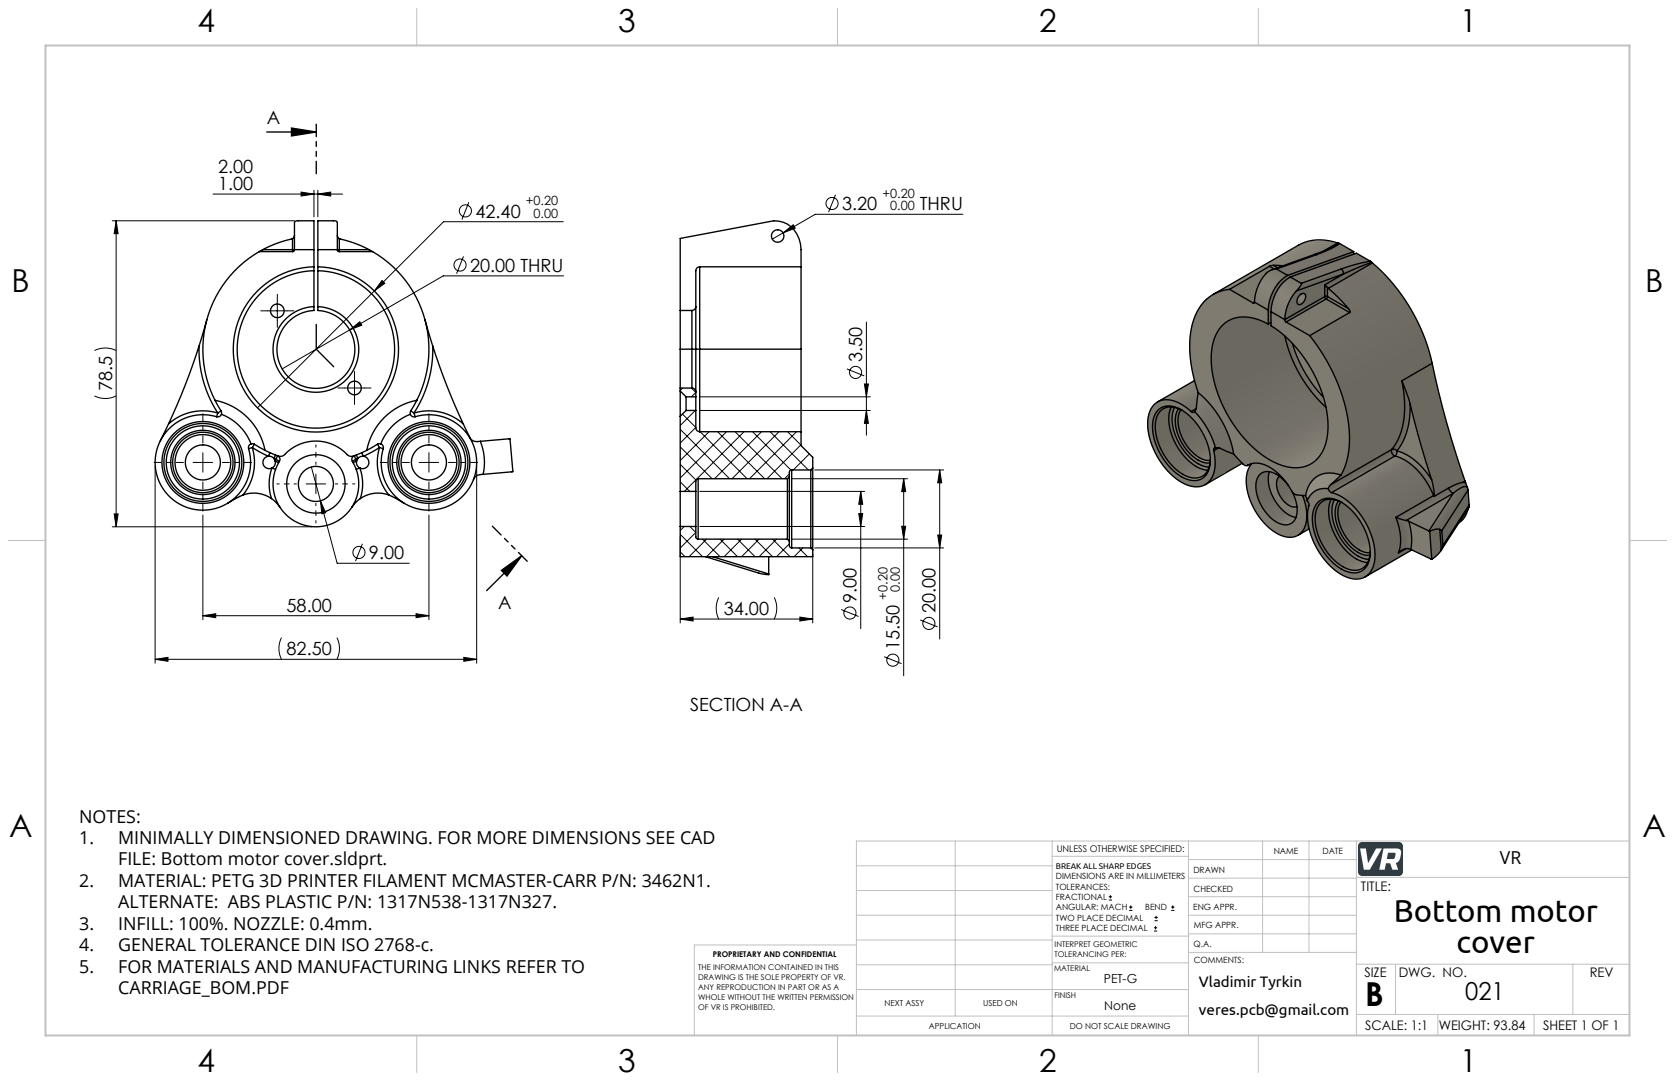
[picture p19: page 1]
20.00 THRU; 0.00 THRU; SECTION A-A; OF VR IS PROHIBITED.; veres.pcb@gmail.com; Vladimir Tyrkin

NOTES:
1. MINIMALLY DIMENSIONED DRAWING. FOR MORE DIMENSIONS SEE CAD
FILE: Bottom motor cover.sldprt.
2. MATERIAL: PETG 3D PRINTER FILAMENT MCMASTER-CARR P/N: 3462N1.
ALTERNATE: ABS PLASTIC P/N: 1317N538-1317N327.
3. INFILL: 100%. NOZZLE: 0.4mm.
4. GENERAL TOLERANCE DIN ISO 2768-c.
5. FOR MATERIALS AND MANUFACTURING LINKS REFER TO
CARRIAGE_BOM.PDF

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

CHECKED | | TITLE: Bottom motor cover

ENG APPR.
MFG APPR.

INTERPRET GEOMETRIC TOLERANCING PER: | Q.A.
MATERIAL PET-G | | SIZE B | DWG. NO. 021 | REV

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

NEXT ASSY | USED ON | None FINISH

APPLICATION | DO NOT SCALE DRAWING | | SCALE: 1:1 | WEIGHT: 93.84 | SHEET 1 OF 1

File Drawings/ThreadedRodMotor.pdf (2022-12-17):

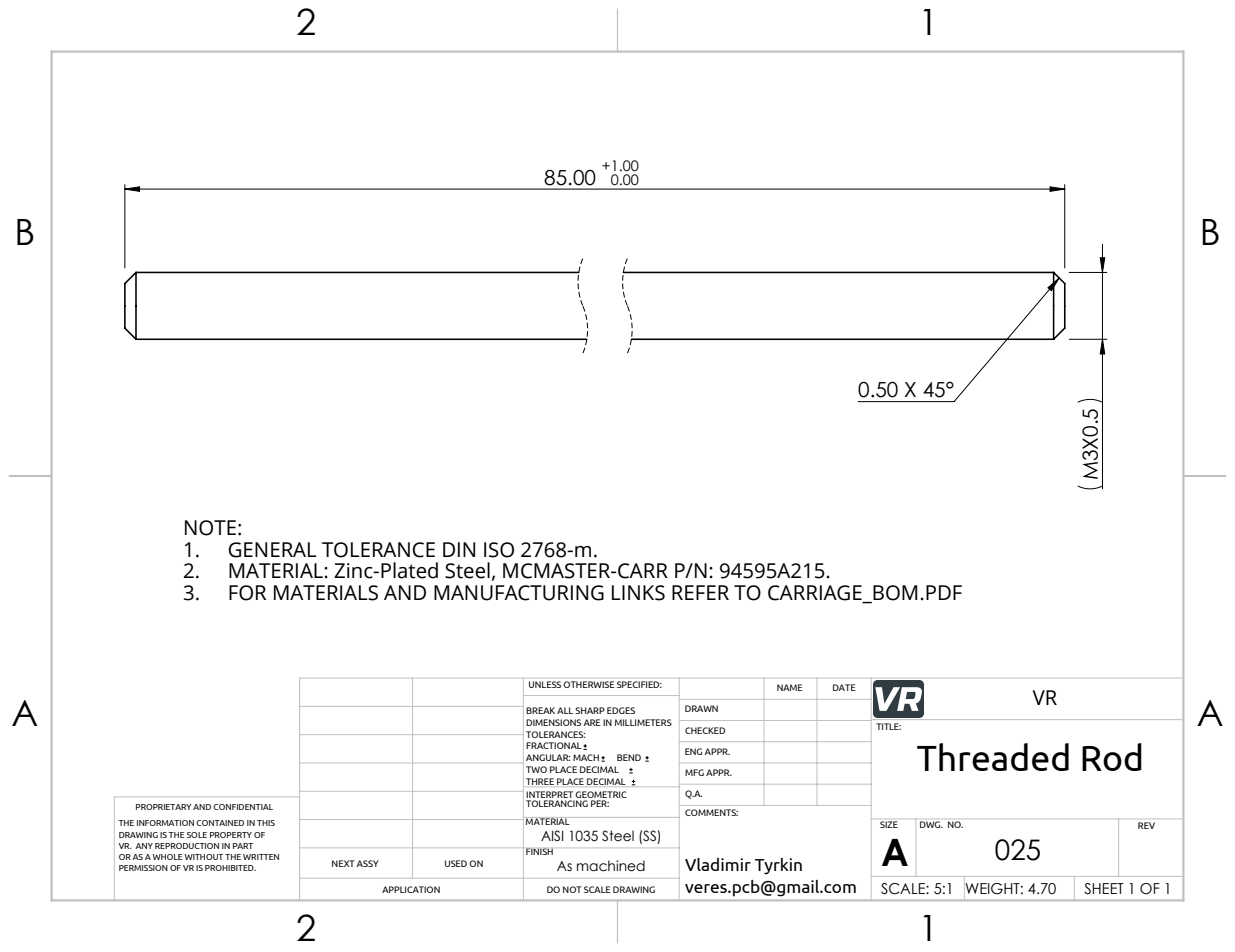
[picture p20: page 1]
PERMISSION OF VR IS PROHIBITED.; Vladimir Tyrkin

NOTE:
1. GENERAL TOLERANCE DIN ISO 2768-m.
2. MATERIAL: Zinc-Plated Steel, MCMASTER-CARR P/N: 94595A215.
3. FOR MATERIALS AND MANUFACTURING LINKS REFER TO CARRIAGE_BOM.PDF

UNLESS OTHERWISE SPECIFIED: | | DATE | VR NAME

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

CHECKED | | TITLE: Threaded Rod

ENG APPR.

MFG APPR.

INTERPRET GEOMETRIC TOLERANCING PER: | Q.A.
MATERIAL AISI 1035 Steel (SS) | | SIZE A | DWG. NO. 025 | REV

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

NEXT ASSY | USED ON | FINISH As machined

APPLICATION | DO NOT SCALE DRAWING | | SCALE: 5:1 | WEIGHT: 4.70 | SHEET 1 OF 1

veres.pcb@gmail.com

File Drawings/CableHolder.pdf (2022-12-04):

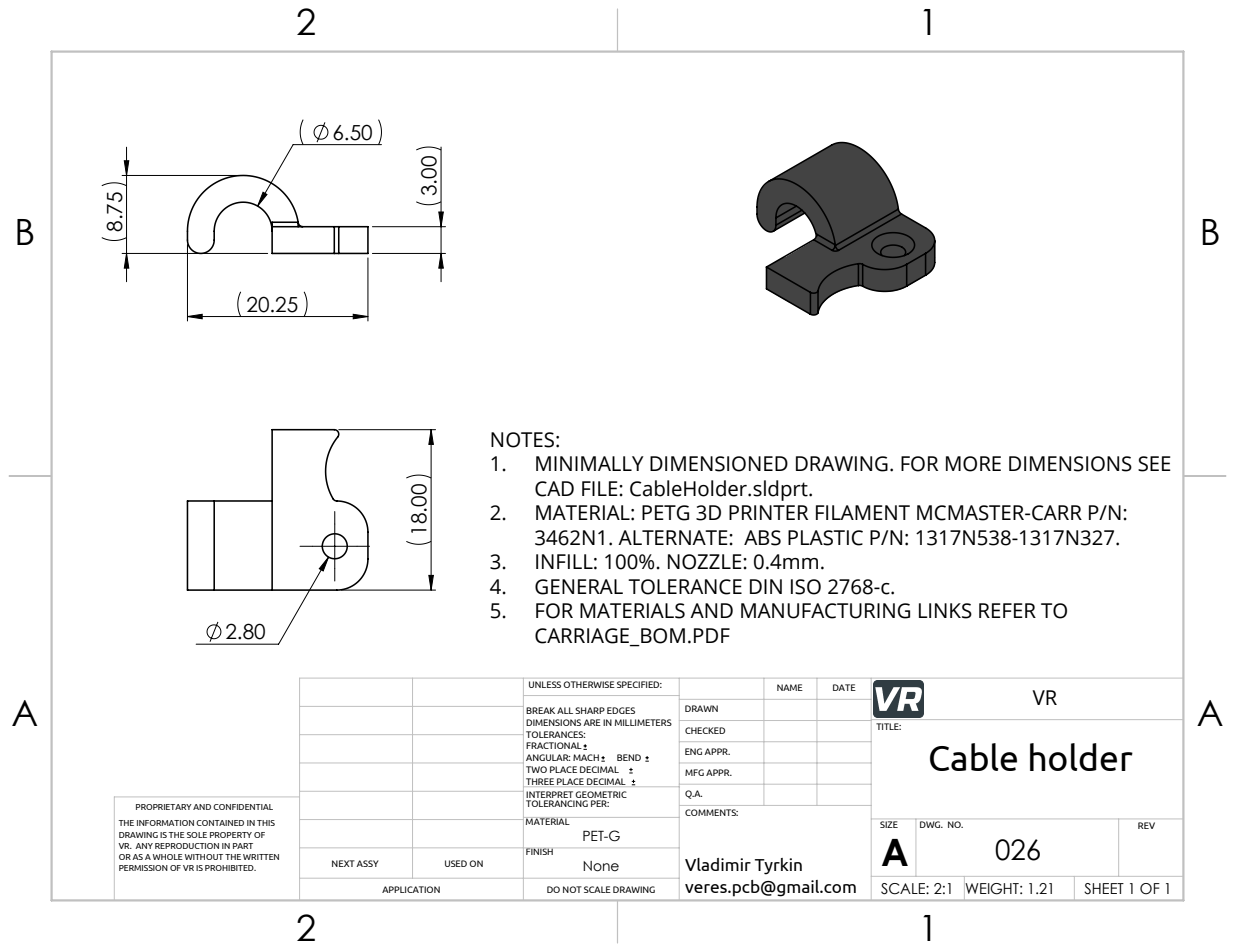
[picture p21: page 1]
PERMISSION OF VR IS PROHIBITED.; Vladimir Tyrkin

NOTES:
1. MINIMALLY DIMENSIONED DRAWING. FOR MORE DIMENSIONS SEE
CAD FILE: CableHolder.sldprt.
2. MATERIAL: PETG 3D PRINTER FILAMENT MCMASTER-CARR P/N:
3462N1. ALTERNATE: ABS PLASTIC P/N: 1317N538-1317N327.
3. INFILL: 100%. NOZZLE: 0.4mm.
4. GENERAL TOLERANCE DIN ISO 2768-c.
5. FOR MATERIALS AND MANUFACTURING LINKS REFER TO
CARRIAGE_BOM.PDF

UNLESS OTHERWISE SPECIFIED: | | DATE | VR NAME

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

CHECKED | | TITLE: Cable holder

ENG APPR.

MFG APPR.

INTERPRET GEOMETRIC TOLERANCING PER: | Q.A.
MATERIAL PET-G | | SIZE A | DWG. NO. 026 | REV

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

NEXT ASSY | USED ON | FINISH None

APPLICATION | DO NOT SCALE DRAWING | | SCALE: 2:1 | WEIGHT: 1.21 | SHEET 1 OF 1

veres.pcb@gmail.com

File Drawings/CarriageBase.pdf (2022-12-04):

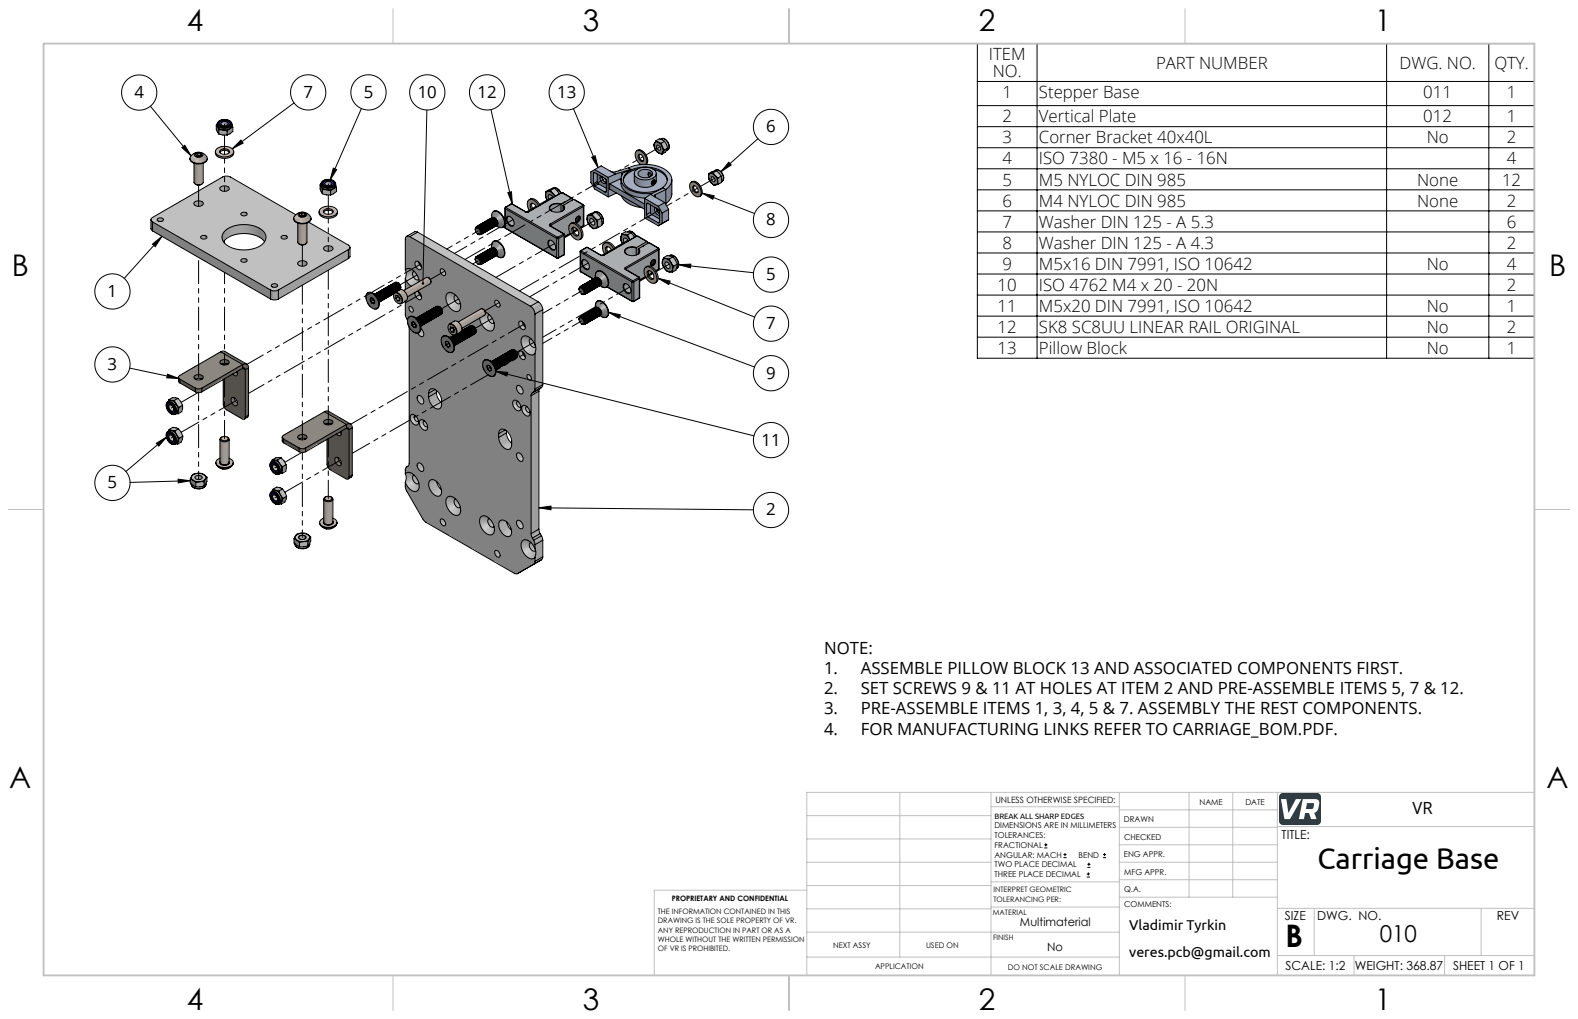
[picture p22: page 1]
OF VR IS PROHIBITED.; veres.pcb@gmail.com; Vladimir Tyrkin

ITEM NO. | PART NUMBER | DWG. NO. | QTY.
1 | Stepper Base | 011 | 1
2 | Vertical Plate | 012 | 1
3 | Corner Bracket 40х40L | No | 2
4 | ISO 7380 - M5 x 16 - 16N | | 4
5 | M5 NYLOC DIN 985 | None | 12
6 | M4 NYLOC DIN 985 | None | 2
7 | Washer DIN 125 - A 5.3 | | 6
8 | Washer DIN 125 - A 4.3 | | 2
9 | M5x16 DIN 7991, ISO 10642 | No | 4
10 | ISO 4762 M4 x 20 - 20N | | 2
11 | M5x20 DIN 7991, ISO 10642 | No | 1
12 | SK8 SC8UU LINEAR RAIL ORIGINAL | No | 2
13 | Pillow Block | No | 1

NOTE:
1. ASSEMBLE PILLOW BLOCK 13 AND ASSOCIATED COMPONENTS FIRST.
2. SET SCREWS 9 & 11 AT HOLES AT ITEM 2 AND PRE-ASSEMBLE ITEMS 5, 7 & 12.
3. PRE-ASSEMBLE ITEMS 1, 3, 4, 5 & 7. ASSEMBLY THE REST COMPONENTS.
4. FOR MANUFACTURING LINKS REFER TO CARRIAGE_BOM.PDF.

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

CHECKED | | TITLE: Carriage Base

ENG APPR.
MFG APPR.

INTERPRET GEOMETRIC TOLERANCING PER: | Q.A.
MATERIAL Multimaterial | | SIZE B | DWG. NO. 010 | REV

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

NEXT ASSY | USED ON | No FINISH

APPLICATION | DO NOT SCALE DRAWING | | SCALE: 1:2 | WEIGHT: 368.87 | SHEET 1 OF 1

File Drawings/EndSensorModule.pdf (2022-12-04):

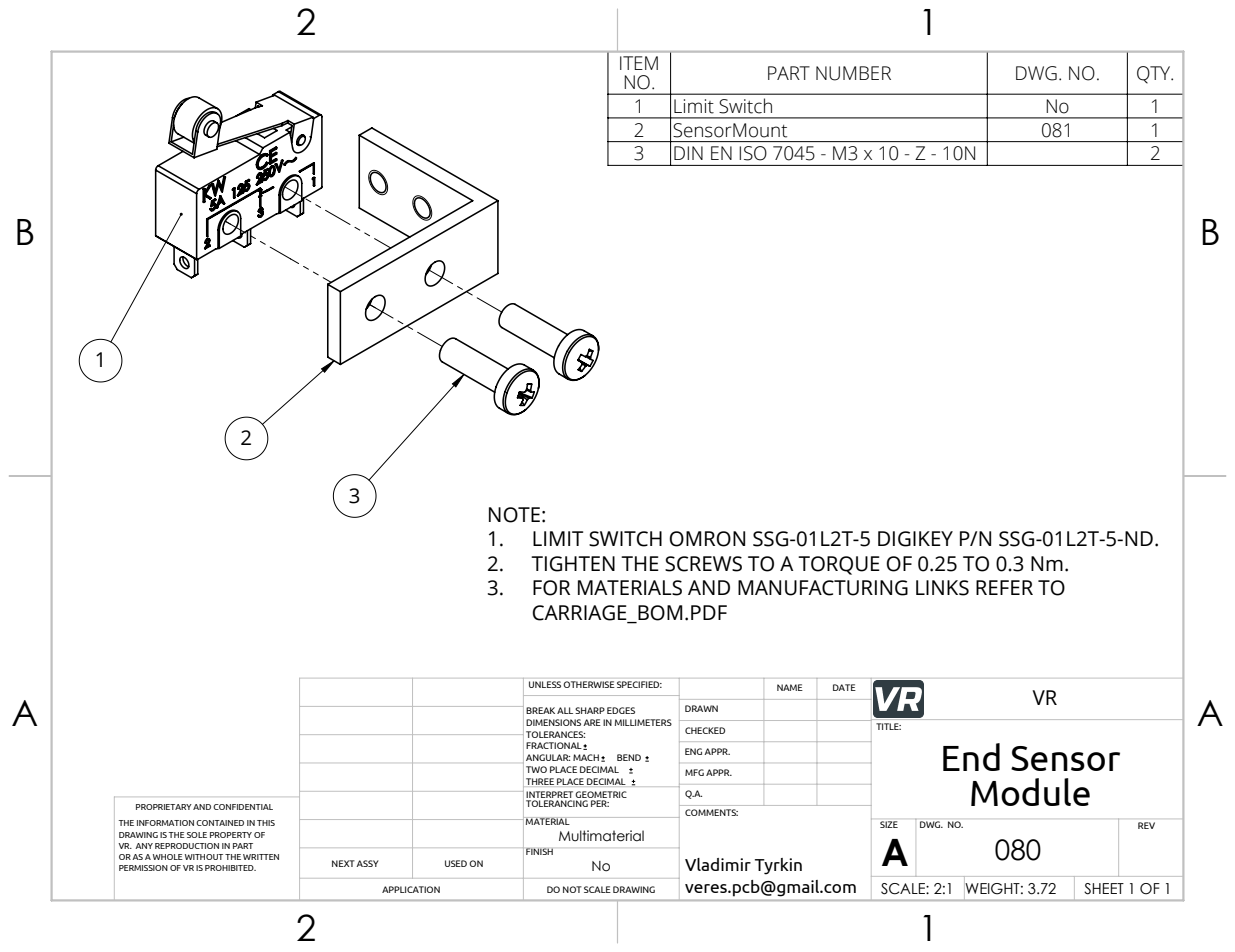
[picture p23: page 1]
PERMISSION OF VR IS PROHIBITED.; Vladimir Tyrkin

ITEM NO. | PART NUMBER | DWG. NO. | QTY.
1 | Limit Switch | No | 1
2 | SensorMount | 081 | 1
3 | DIN EN ISO 7045 - M3 x 10 - Z - 10N | | 2

NOTE:
1. LIMIT SWITCH OMRON SSG-01L2T-5 DIGIKEY P/N SSG-01L2T-5-ND.
2. TIGHTEN THE SCREWS TO A TORQUE OF 0.25 TO 0.3 Nm.
3. FOR MATERIALS AND MANUFACTURING LINKS REFER TO
CARRIAGE_BOM.PDF

UNLESS OTHERWISE SPECIFIED: | | DATE | VR NAME

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

CHECKED | | TITLE: End Sensor Module

ENG APPR.

MFG APPR.

INTERPRET GEOMETRIC TOLERANCING PER: | Q.A.
MATERIAL Multimaterial | | SIZE A | DWG. NO. 080 | REV

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

NEXT ASSY | USED ON | FINISH No

APPLICATION | DO NOT SCALE DRAWING | | SCALE: 2:1 | WEIGHT: 3.72 | SHEET 1 OF 1

veres.pcb@gmail.com

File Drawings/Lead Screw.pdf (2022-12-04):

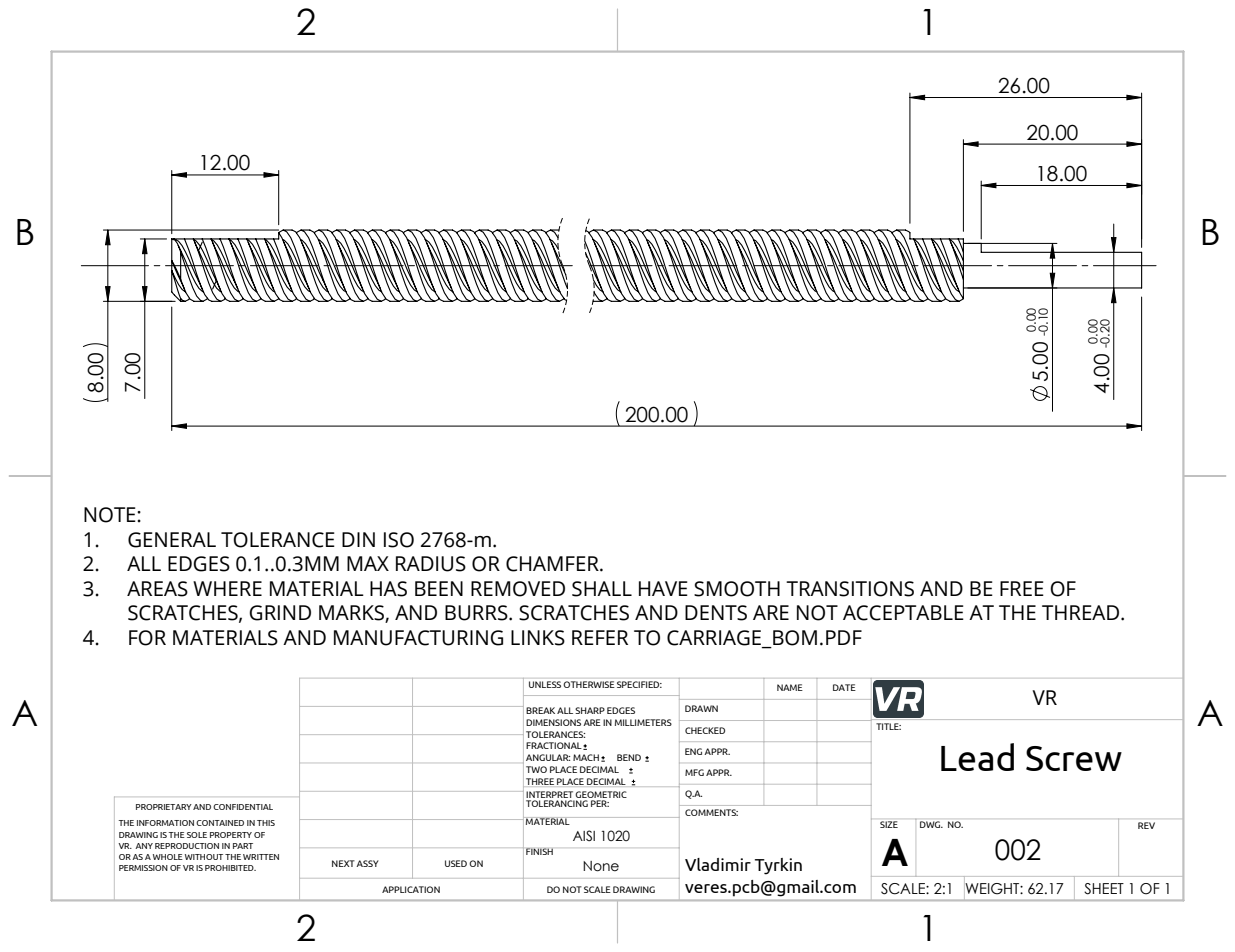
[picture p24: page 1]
PERMISSION OF VR IS PROHIBITED.; Vladimir Tyrkin

NOTE:
1. GENERAL TOLERANCE DIN ISO 2768-m.
2. ALL EDGES 0.1..0.3MM MAX RADIUS OR CHAMFER.
3. AREAS WHERE MATERIAL HAS BEEN REMOVED SHALL HAVE SMOOTH TRANSITIONS AND BE FREE OF
SCRATCHES, GRIND MARKS, AND BURRS. SCRATCHES AND DENTS ARE NOT ACCEPTABLE AT THE THREAD.
4. FOR MATERIALS AND MANUFACTURING LINKS REFER TO CARRIAGE_BOM.PDF

UNLESS OTHERWISE SPECIFIED: | | DATE | VR NAME

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

CHECKED | | TITLE: Lead Screw

ENG APPR.

MFG APPR.

INTERPRET GEOMETRIC TOLERANCING PER: | Q.A.
MATERIAL AISI 1020 | | SIZE A | DWG. NO. 002 | REV

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

NEXT ASSY | USED ON | FINISH None

APPLICATION | DO NOT SCALE DRAWING | | SCALE: 2:1 | WEIGHT: 62.17 | SHEET 1 OF 1

veres.pcb@gmail.com

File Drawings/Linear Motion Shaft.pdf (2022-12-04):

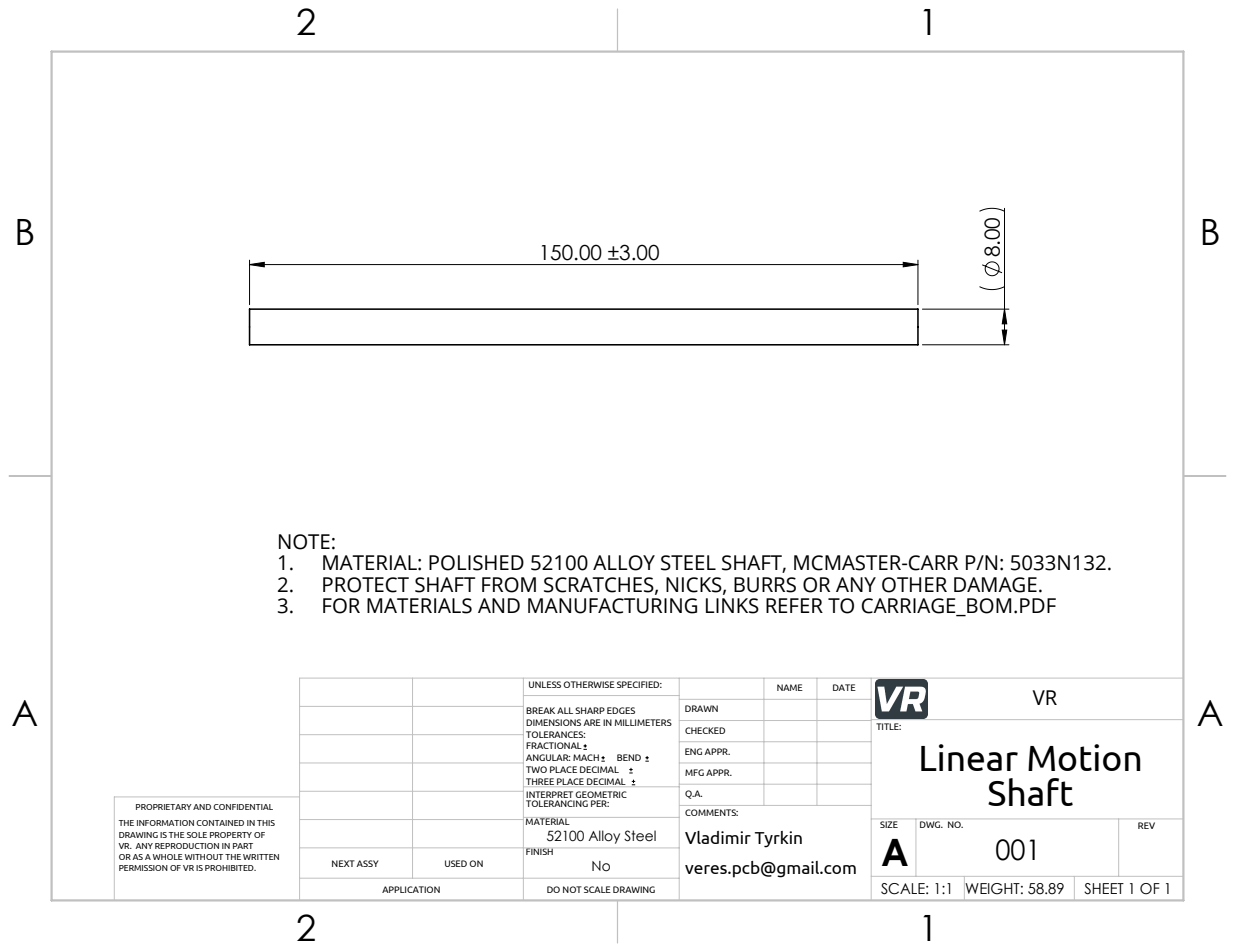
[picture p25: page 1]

NOTE:
1. MATERIAL: POLISHED 52100 ALLOY STEEL SHAFT, MCMASTER-CARR P/N: 5033N132.
2. PROTECT SHAFT FROM SCRATCHES, NICKS, BURRS OR ANY OTHER DAMAGE.
3. FOR MATERIALS AND MANUFACTURING LINKS REFER TO CARRIAGE_BOM.PDF

UNLESS OTHERWISE SPECIFIED: | | DATE | VR NAME

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

CHECKED | | TITLE: Linear Motion Shaft

ENG APPR.

MFG APPR.

INTERPRET GEOMETRIC TOLERANCING PER: | Q.A.
MATERIAL 52100 Alloy Steel | | SIZE A | DWG. NO. 001 | REV

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

COMMENTS:
Vladimir Tyrkin
veres.pcb@gmail.com

NEXT ASSY | USED ON | FINISH No

APPLICATION | DO NOT SCALE DRAWING | | SCALE: 1:1 | WEIGHT: 58.89 | SHEET 1 OF 1

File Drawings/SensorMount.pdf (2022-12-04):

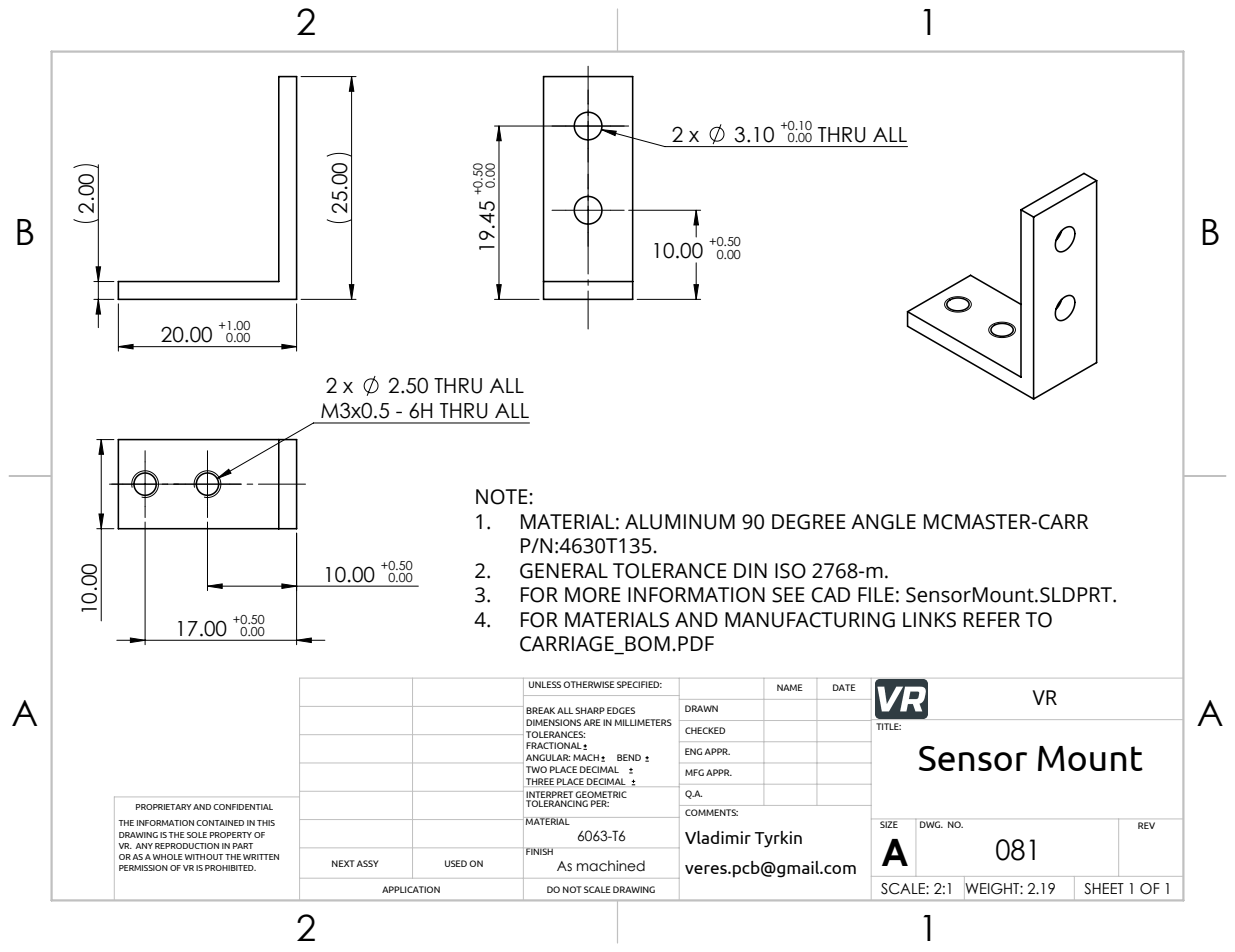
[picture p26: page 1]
2.50 THRU ALL; M3x0.5 - 6H THRU ALL; 0.00 THRU ALL

NOTE:
1. MATERIAL: ALUMINUM 90 DEGREE ANGLE MCMASTER-CARR
2. GENERAL TOLERANCE DIN ISO 2768-m.
3. FOR MORE INFORMATION SEE CAD FILE: SensorMount.SLDPRT.
4. FOR MATERIALS AND MANUFACTURING LINKS REFER TO
CARRIAGE_BOM.PDF

UNLESS OTHERWISE SPECIFIED: | | DATE | VR NAME

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

CHECKED | | TITLE: Sensor Mount

ENG APPR.

MFG APPR.

INTERPRET GEOMETRIC TOLERANCING PER: | Q.A.
MATERIAL 6063-T6 | | SIZE A | DWG. NO. 081 | REV

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

COMMENTS:
Vladimir Tyrkin
veres.pcb@gmail.com

NEXT ASSY | USED ON | FINISH As machined

APPLICATION | DO NOT SCALE DRAWING | | SCALE: 2:1 | WEIGHT: 2.19 | SHEET 1 OF 1

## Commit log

2020-12-20 Some little bugs fixed
    [ER11 collet.SLDASM]
2021-01-02 Update files to SW2020. Some composition changes. Added more fasteners
    [1LX3.2.512.SLDPRT, 2GT_20T_Toothed_5mmBore.SLDPRT, Carriage Y_2.SLDPRT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]
2021-01-03 Some little composition changes.
    [Lead screw T8X8X400.SLDASM, Low Profile Hex Screw M5x30.SLDPRT]
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2021-01-03 Change position of end sensors
    [Lead screw T8X8X400.SLDASM]
2021-01-03 Decrease width of the CarriageBase
    [Lead screw T8X8X400.SLDASM]
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2021-01-05 Replace some screws
    [Lead screw T8X8X400.SLDASM, Low Profile Hex Screw M5x30.SLDPRT]
2021-01-05 Change geometry a little bit & add new screws
    [Lead screw T8X8X400.SLDASM]
2021-01-07 Added ventilation holes to carriage. Updated encoder
    [Lead Screw T8X8X400.sldprt, Lead screw T8X8X400.SLDASM]
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2021-01-10 A little changes in carriage cower
    [AnotherCarriageZ.SLDPRT, Corner Bracket 40х40L.SLDPRT]
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2021-01-20 Changed lead screw length. Added some wires
    [Lead Screw T8X8X400.sldprt, Lead screw T8X8X400.SLDASM]
2021-01-22 A little changes with cables and encoder
    [AnotherCarriageZ.SLDPRT, Lead screw T8X8X400.SLDASM]
2021-01-30 Added mount to encoder
    [Lead screw T8X8X400.SLDASM]
2021-01-31 Added motor & encoder wires
    [Lead screw T8X8X400.SLDASM]
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2021-05-12 Updated the readme file
    [D6.d6.lenght75.SLDPRT]
2021-05-21 Updated some parts. Added a drawing for sensor mount
    [EndSensorAluminumMount.SLDDRW, EndSensorAluminumMount.SLDPRT]
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2021-06-09 Added drawings, updated material properties and tolerances in the parts. Added BOM
    [Rod.SLDPRT, SpacerForCarriage.SLDDRW, SpacerForCarriage.SLDPRT]
2021-06-12 Updated properties in the parts and the assemblies, updated the BOM. Added internet links to some positions in the BOM
    [2GT_20T_Toothed_5mmBore.SLDPRT, AnotherCarriageZ.SLDPRT, Corner Bracket 40х40L.SLDPRT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]
2021-06-13 Added cable to the stepper, updated end sensor wire
    [Lead screw T8X8X400.SLDASM, Stepper QK1-1032.SLDPRT]
2021-06-23 Added a scheme and a pcb for encoder
    [Encoder.brd, Encoder.sch]
2021-06-27 Added a pcb for encoder: made scheme, library and prearranged components on the board
    [Encoder.brd, Encoder.sch]
2021-06-27 Updated the assembly in case of encoder: added a pcb and updated the cover
    [ITR-9608.SLDPRT, Low Profile Hex Screw M5x30.SLDPRT]
2021-06-30 Added connector for programmer. Increased the place for the encoder.
    [Encoder.brd, Encoder.sch]
2021-08-06 Added more powerful stepper motor
    [Lead screw T8X8X400.SLDASM]
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2021-08-21 Updated the tensioner. Made TensionerBasePlate as a real part, updated properties, made drawing
    [TensionerBasePlate.SLDDRW, TensionerBasePlate.SLDPRT]
2021-08-27 Updated the dimensions and tolerances in the tensioner plate. Updated some parameters in the parts.
    [SpacerForCarriage.SLDPRT, TensionerBasePlate.SLDPRT]
2021-08-28 Updated properties for some parts. Updated tolerances. Added drawing numbers. Added some drawings
    [ER11 collet.SLDASM, EndSensorAluminumMount.SLDPRT, GT2 16 Teeth Pulley 3mm dia.SLDPRT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]
2021-08-29 Updated mount in motor holder
    [1LX3.2.512.SLDPRT, 2GT_20T_Toothed_5mmBore.SLDPRT, AnotherCarriageZ.SLDPRT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]
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2021-11-07 Added drawing for the tensioner and made it non virtual
    [Lead screw T8X8X400.SLDASM, Tensioner2.SLDASM, Tensioner2.SLDDRW]
2021-11-07 Added drawing for Carriage
    [CarriageBase.SLDASM, CarriageBase.SLDDRW, Lead screw T8X8X400.SLDASM]
2021-11-10 Updated the plastic mount brackets in the carriage
    [CarriageBase.SLDASM, Lead screw T8X8X400.SLDASM, SpacerForCarriage.SLDPRT]
2021-11-11 Updated spacers and another part of the carriage
    [AnotherCarriageZ.SLDPRT, CarriageBase.SLDASM, Lead screw T8X8X400.SLDASM]
2021-11-20 Updated material in plastic parts.
    [AnotherCarriageZ.SLDPRT, CarriageBase.SLDASM, Lead screw T8X8X400.SLDASM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]
2021-12-17 Packed all files into a single directory.
    [1LX3.2.512.SLDPRT, 2GT_20T_Toothed_5mmBore.SLDPRT, AnotherCarriageZ.SLDPRT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]
2021-12-18 Updated preview. Removed unnecessary stepper motor.
    [Stepper QK1-1032.SLDPRT]
2022-01-02 Updated the main assembly structure. Updated drawings.
    [CarriageBase.SLDASM, CarriageBase.SLDDRW, EndSensorAluminumMount.SLDPRT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]
2022-01-02 Updated the main assembly structure. Moved some parts between subassemblies. Updated the main drawing.
    [CarriageBase.SLDASM, KP08 _ А.01.111.SLDPRT, Pillow Block KP08.SLDPRT]
2022-01-04 Replaced some screws, updated drawings.
    [92125A212_18-8 Stainless Steel Hex Drive Flat Head Screw.SLDPRT, CarriageBase.SLDASM]
2022-01-05 Changed exploded views, updated drawings.
    [39014031.SLDPRT, 39014033.SLDPRT, CarriageBase.SLDASM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]
2022-01-06 Saved some parts as non virtual, added drawings
    [AnotherCarriageZ.SLDPRT, CarriageBase.SLDASM, Spacer for cover.SLDPRT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]
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2022-02-05 Updated structure, parts and drawings.
    [Bottom motor cover.SLDDRW, Bottom motor cover.SLDPRT, CarriageBase.SLDASM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]
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2022-02-10 Updated drawings and part properties.
    [CarriageBase.SLDASM, CarriageBase.SLDDRW, EndSensorModule.SLDASM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]
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2022-03-16 Added all drawings file and 3d pdf file
    [Bearing Subassy, GT2 Idler Pulley, Configurable.SLDASM, CarriageBase.SLDASM, EndSensorModule.SLDASM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]
2022-06-25 added some chamfers, removed some geometry for best printing. updated parameter isFastener in parts
    [2GT_20T_Toothed_5mmBore.SLDPRT, 39014031.SLDPRT, 99461A947_Phillips Rounded Head Thread-Forming Screws.SLDPRT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]
2022-08-14 some little changes. added drawings for polycarbonate production
    [Bearing Subassy, GT2 Idler Pulley, Configurable.SLDASM, CarriageBase.SLDASM, EndSensorModule.SLDASM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]
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2022-10-01 updated screws nut and motor cower. Updated the tensioner assembly.
    [Bearing Subassy, GT2 Idler Pulley, Configurable.SLDASM, Bottom motor cover.SLDPRT, CarriageBase.SLDASM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]
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2023-01-01 fixed some bugs
    [Bottom motor cover.SLDPRT, CARRIAGE_BOM.xlsx, CarriageBase.SLDASM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]
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
